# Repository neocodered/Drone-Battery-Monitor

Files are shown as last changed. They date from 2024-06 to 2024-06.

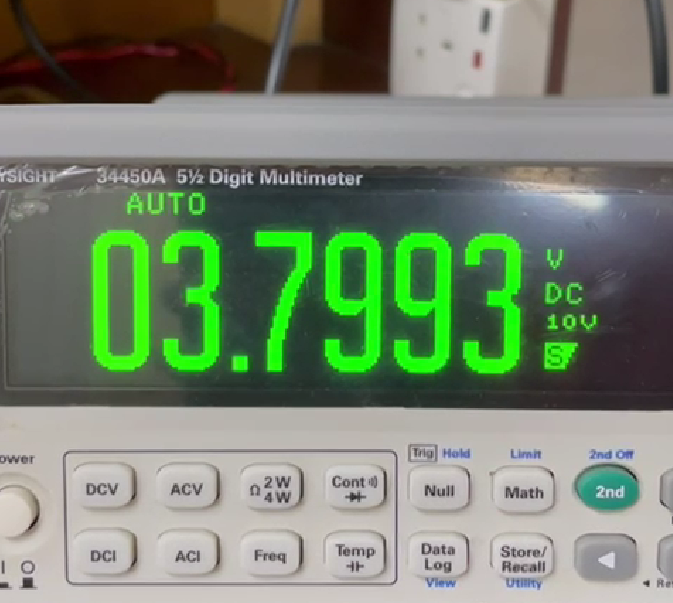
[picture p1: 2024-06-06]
With voltage readings only/Oscilloscope readings from the voltage output/Voltage_drop_motor.png

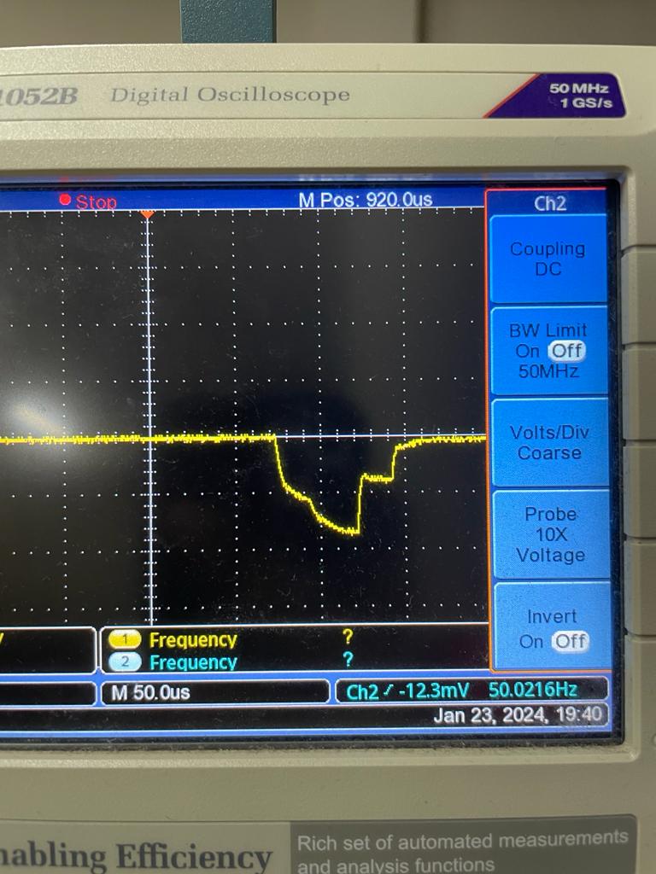
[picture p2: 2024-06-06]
With voltage readings only/Oscilloscope readings from the voltage output/Zoomed in signal waaveform.jpeg

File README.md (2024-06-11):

# Drone Battery Monitor
**Description**:
Developing an advanced battery percentage measurement system for the XFly drone platform to accurately determine remaining battery life and calculate flight time.

**Initial Approach**:
- Measured battery voltage and calibrated sensor readings to reflect actual voltage.
- Faced challenges due to battery voltage instability and sensor noise.
- Utilized a machine learning model with PWM values and voltage readings, but accuracy was limited.

**Current Approach**:
- Designing a module with analog low-pass filters to reduce voltage reading noise.
- Incorporating current measurements to complement voltage data.
- Analyzing voltage and current to calculate the battery's electromotive force (EMF).
- Providing a more reliable estimate of remaining battery capacity.

**Key Objectives**:
- Enhance accuracy of battery life measurement.
- Improve reliability of flight time predictions for the XFly drone platform.
- Develop a dual-parameter system considering both voltage and current for stable battery percentage readings.

This project aims to significantly improve the accuracy and reliability of battery measurement systems for drones, supporting better flight time management and overall performance.

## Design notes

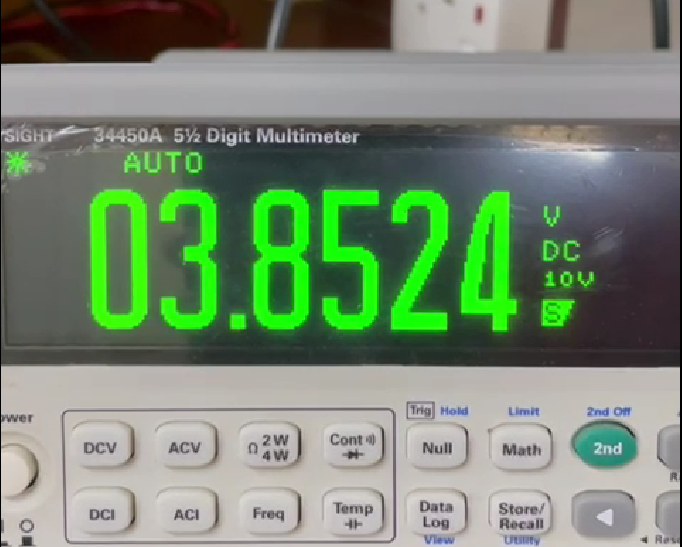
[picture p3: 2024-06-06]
With voltage readings only/Oscilloscope readings from the voltage output/Voltage_normal_motor.png

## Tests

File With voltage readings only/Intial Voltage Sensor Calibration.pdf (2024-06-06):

# Report on voltage fluctuations and how the battery percentage should be measured

## Battery percentage measurement without the motors running

An input related to the battery level can be taken from the I/O pin 1. Using analogRead() we can measure the values.

Value from the analogRead() = X | Voltage of the battery = Y
1226 | 3.81
1242 | 3.87
1260 | 3.92
1275 | 3.97
1355 | 4.22

These data have a Pearson correlation of 0.999746. Hence these data are highly corelated.
Y = -0.04828 + 3.15058*(10^-3)X

Readings can be mapped out to real voltages using this equation.

## Battery percentage measurement when the motors are running

When the motors are running a noise is generated in the reading.

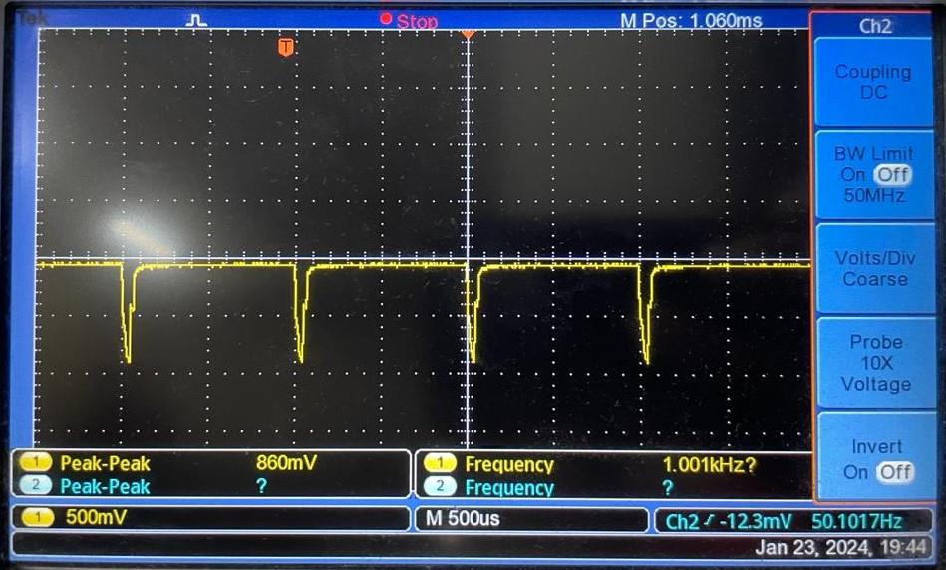
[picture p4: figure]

A periodic wave with a frequency of 1kHz is formed. This noise can be filtered by using a LPF with a cutoff frequency less than 1kHz.

When the motors start running a sudden voltage drop is occurred in the reading.

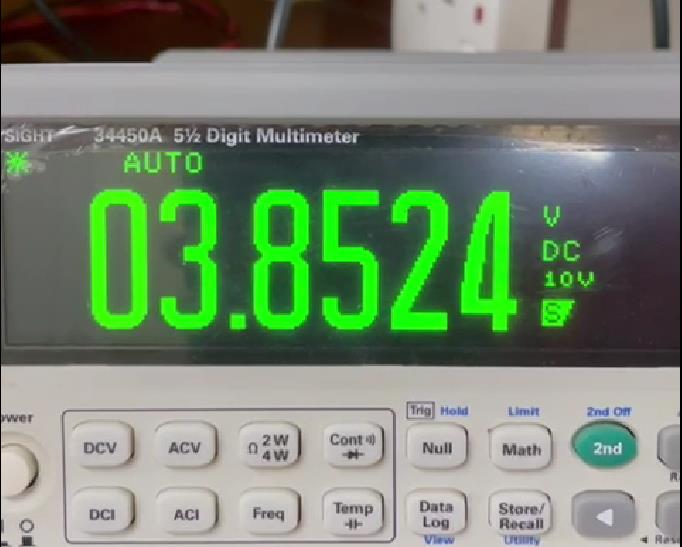
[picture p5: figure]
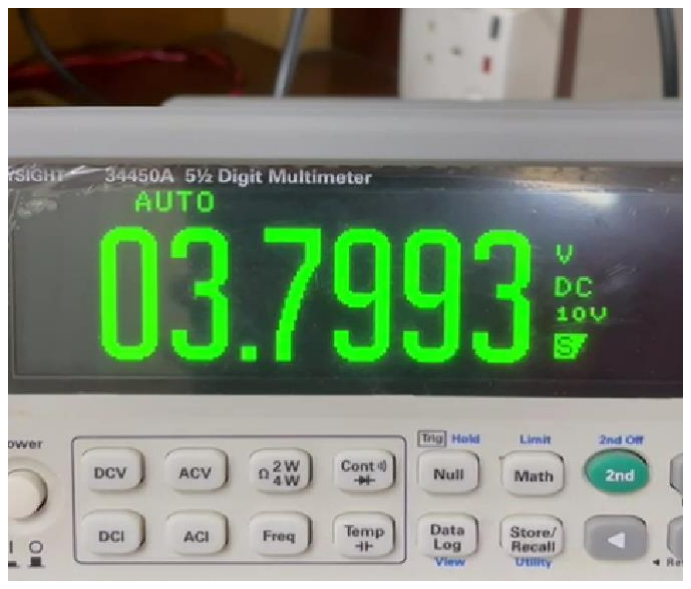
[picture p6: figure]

(Before motors run) | (When motors are running)

This drop varies with the real battery voltage (voltage before the motor runs).

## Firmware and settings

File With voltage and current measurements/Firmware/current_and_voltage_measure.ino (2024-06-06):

#include "motor.h"

float f_voltage;
float f_current;

float current;
float voltage;

float final_voltage;

bool start = true;

float bat_perc;

float prev_perc = 100;

void setup() {

  Serial.begin(9600);
  pinMode(A0,INPUT);
  pinMode(A1,INPUT);
  motor_setup();

  delay(1000);

  // const float in_current = analogRead(A0);
  float in_voltage = analogRead(A1);
  in_voltage = in_voltage*0.02438;

  int a = 0;
  while (true){
    motor_speed(50,50,50,50);

    current = analogRead(A0);
    voltage = analogRead(A1);

    voltage = voltage*0.02438;
    current = current*0.23441;

    f_voltage = 0.9937*f_voltage + 0.006263*voltage;
    f_current = 0.9937*f_current + 0.006263*current;

    a++;
    delay(10);

    if (a >= 1000){
      break;
    }
  }

  motor_speed(0,0,0,0);
  const float r = (in_voltage - f_voltage)/f_current;

  f_voltage = 0;
  f_current = 0;
}

void loop() {
  
  // Getting the values from the sensors
  current = analogRead(A0);
  voltage = analogRead(A1);

  // Adjusting the values by multiplying by relevant tuning coefficients
  voltage = voltage*0.02438;
  current = current*0.23441;

  // Filtering oout the readings
  f_voltage = 0.9937*f_voltage + 0.006263*voltage;
  f_current = 0.9937*f_current + 0.006263*current;

  Serial.print("Current:");
  Serial.print(f_current);
  Serial.print("mA ");
    
  Serial.print("Voltage:");
  Serial.print(f_voltage);
  Serial.println("v");

  final_voltage = f_voltage + f_current*r;

  bat_perc = (final_voltage - 3.7)*100/4.2;

  if (prev_perc < bat_perc){
    bat_perc = prev_perc;
  }

  prev_perc = bat_perc;

  if (bat_perc<0){
    Serial.println("Low_Power");
  }

  delay(50);
}

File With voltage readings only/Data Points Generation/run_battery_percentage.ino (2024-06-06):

#include "motor.h" // Include the motor control functions

float run_voltage;
float stop_voltage;

float voltage(int x){
  return -0.048 + 0.00315*x + 0.01;
}

void setup() {
  Serial.begin(9600); // Start serial communication at 9600 baud rate
  motor_setup();      // Setup the motor
}

void loop() {

  if (voltage(analogRead(1)) > 3.7){
    for (int k = 0; k<1000; k += 50){
      motor_speed(k, k, k, k);
      delay(1000);
      run_voltage = voltage(analogRead(1));
      motor_stop();
      delay(1000);
      if (k==0){
        stop_voltage = voltage(analogRead(1));
      }
      Serial.print(k);
      Serial.print(",");
      Serial.print(run_voltage);
      Serial.print(",");
      Serial.println(stop_voltage);
    }
    for (int k = 1000; k>0; k -= 50){
      motor_speed(k, k, k, k);
      delay(1000);
      run_voltage = voltage(analogRead(1));
      motor_stop();
      delay(1000);
      if (k==0){
        stop_voltage = voltage(analogRead(1));
      }
      Serial.print(k);
      Serial.print(",");
      Serial.print(run_voltage);
      Serial.print(",");
      Serial.println(stop_voltage);
    }
  }
  else{
    motor_stop();
  }

  motor_speed(200, 0, 0, 0);
  Serial.println(voltage(analogRead(1)));
  delay(5000);
  motor_stop()
  delay(5000)
  motor_speed(200, 200, 0, 0);
  delay(5000);
  motor_stop()
  delay(5000)
}
